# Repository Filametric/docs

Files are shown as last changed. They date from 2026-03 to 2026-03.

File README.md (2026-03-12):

# Filametric Docs

Official documentation for the Filametric DryBase, built with [MkDocs Material](https://squidfunk.github.io/mkdocs-material/).

**Live at:** [docs.filametric.com](https://docs.filametric.com)

## Local development

```bash
pip install mkdocs-material mkdocs-git-revision-date-localized-plugin
mkdocs serve
```

## Deployment

Automatic via GitHub Actions on every push to `main`.

## License

Documentation content © 2026 Filametric B.V. All rights reserved.

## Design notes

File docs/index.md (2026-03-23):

---
hide:
  - navigation
---

# Filametric Documentation

<div class="print-grid" markdown>

<a class="print-card" href="manual/introduction/">
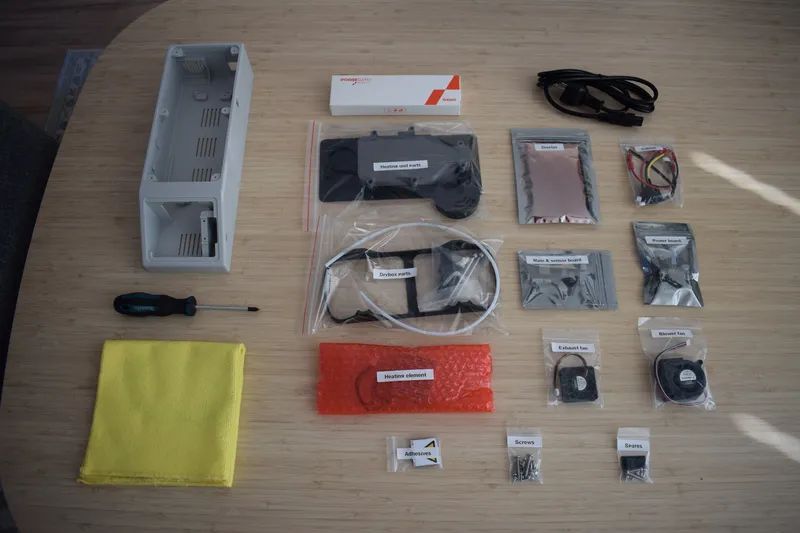
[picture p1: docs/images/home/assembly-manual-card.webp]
Assembly Manual
  
  <span>Assembly Manual</span>
</a>

<a class="print-card" href="3d-printing/guide/">
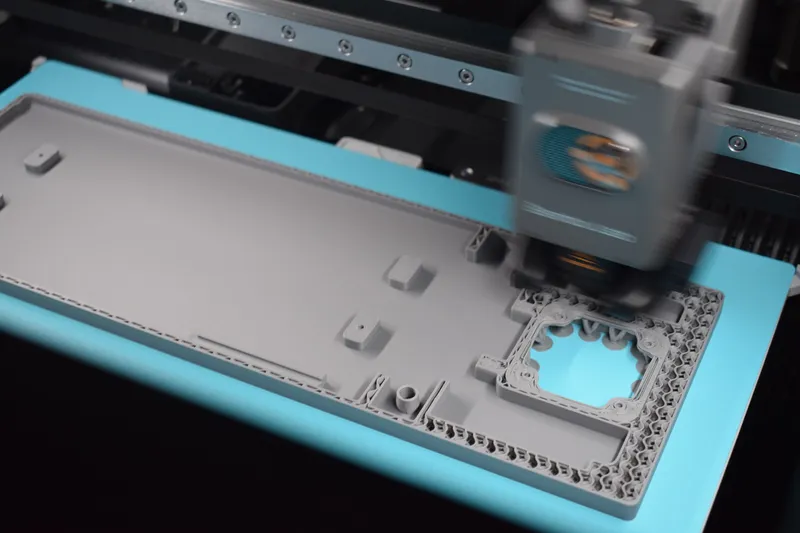
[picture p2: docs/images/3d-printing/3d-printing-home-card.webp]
3D Printing
  
  <span>3D Printing</span>
</a>

<a class="print-card" href="drybase/overview/">
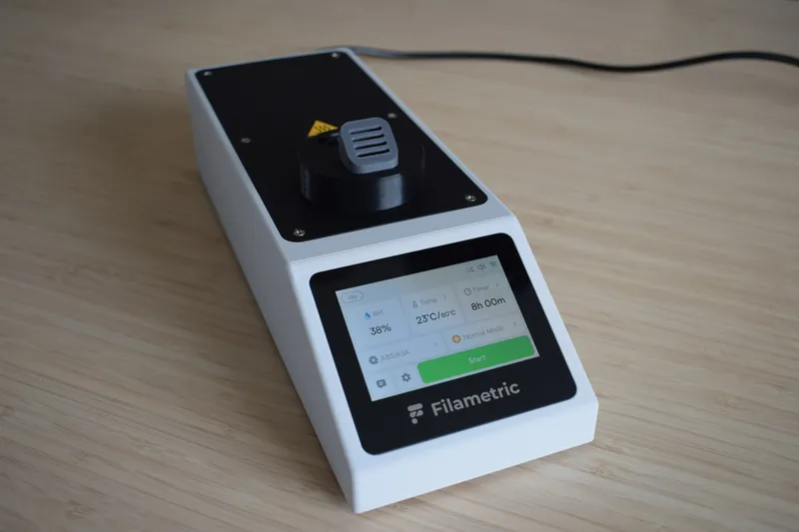
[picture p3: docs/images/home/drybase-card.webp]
DryBase
  
  <span>DryBase</span>
</a>

<a class="print-card" href="drybox/overview/">
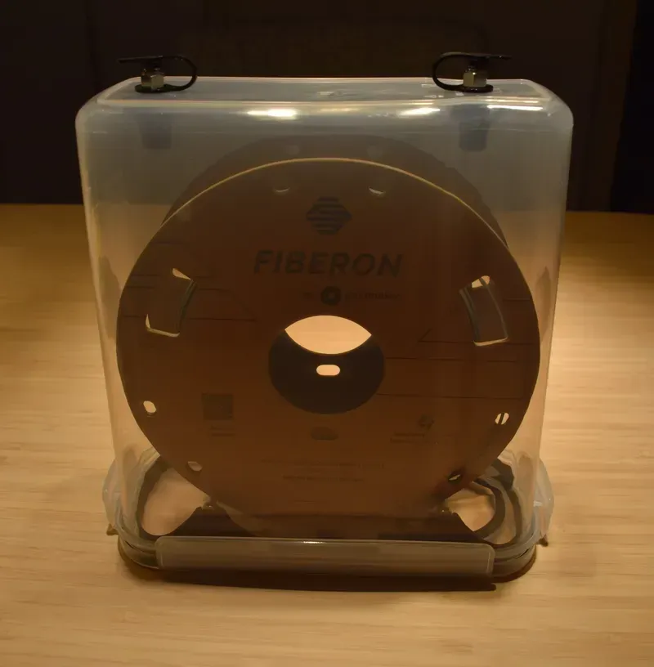
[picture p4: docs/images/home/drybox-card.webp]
Drybox
  
  <span>Drybox</span>
</a>

<a class="print-card" href="studio/overview/">
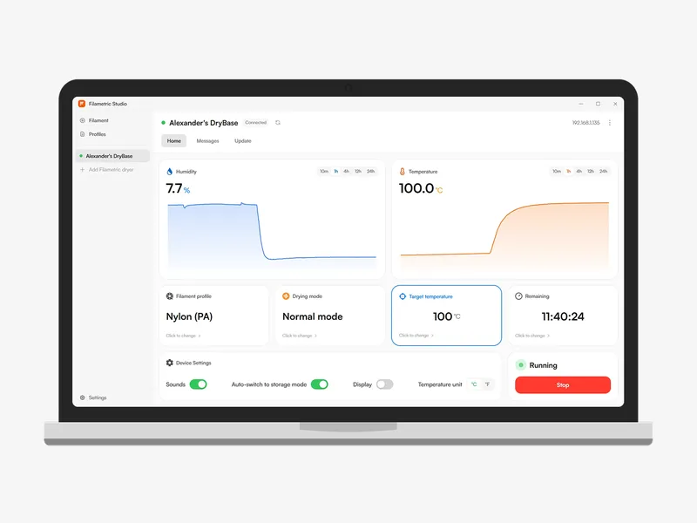
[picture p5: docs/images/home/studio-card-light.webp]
Filametric Studio
  
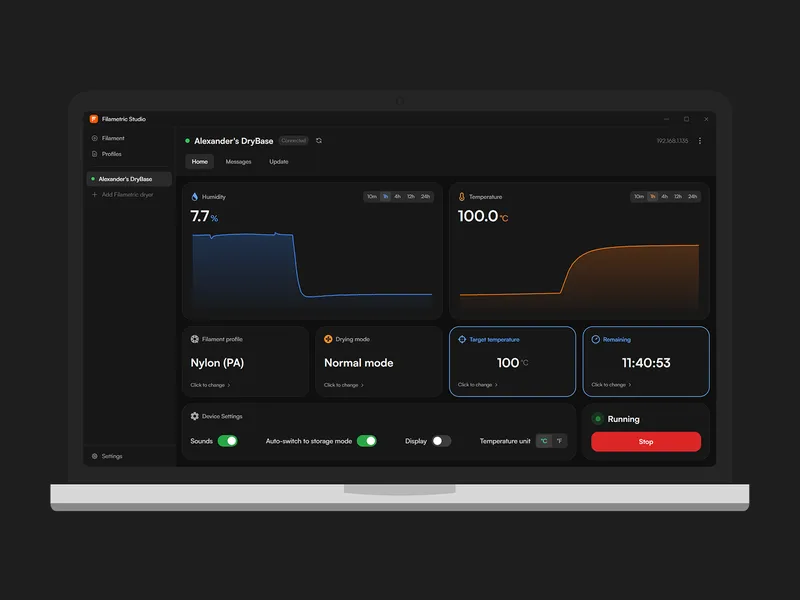
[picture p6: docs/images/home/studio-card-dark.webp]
Filametric Studio
  
  <span>Filametric Studio</span>
</a>

<a class="print-card" href="support/faq/">
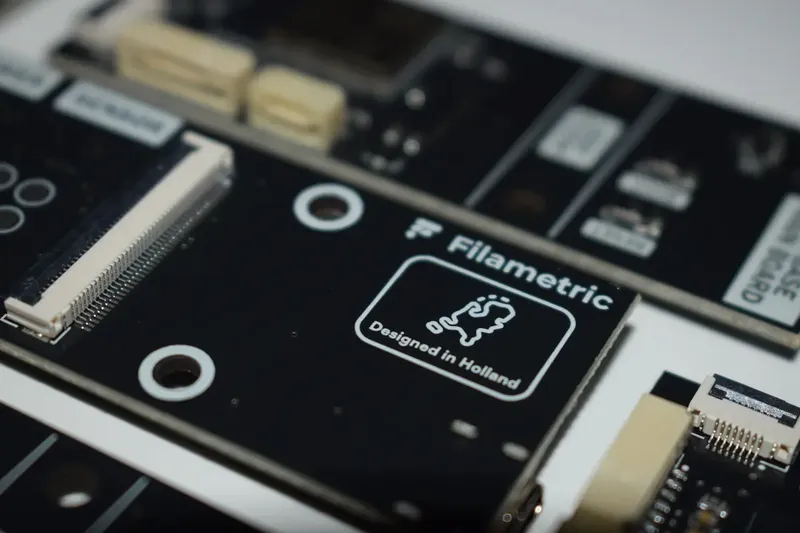
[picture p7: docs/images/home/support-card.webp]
Support
  
  <span>Support</span>
</a>

</div>

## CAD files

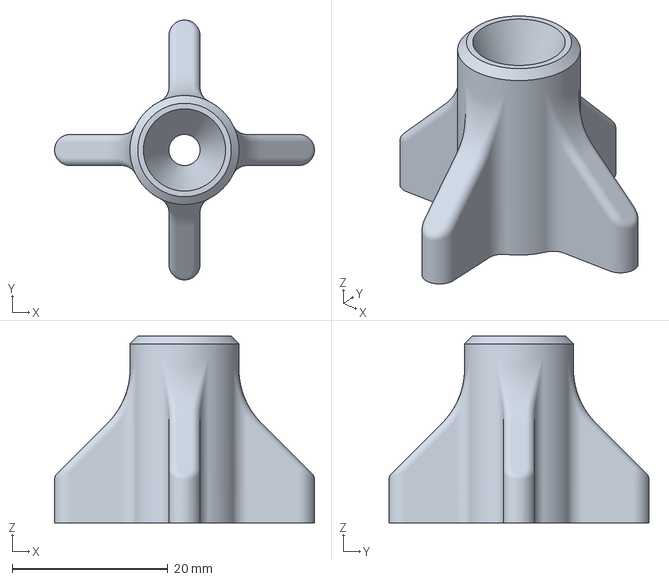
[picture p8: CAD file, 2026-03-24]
docs/downloads/Filametric_Closing_Fastener_3MF.3mf
33.4 x 33.4 x 24.0 mm

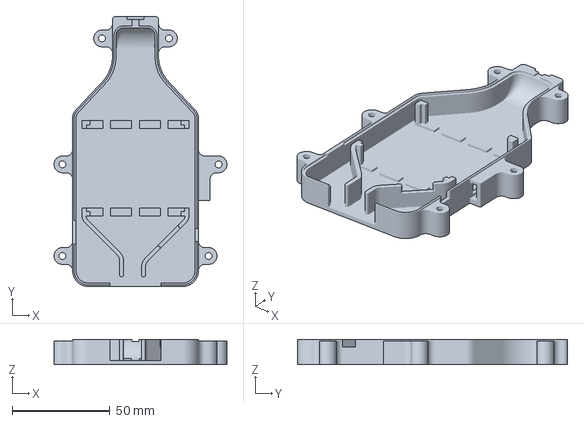
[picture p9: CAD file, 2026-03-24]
docs/downloads/Filametric_Heating_Element_Bottom_Cover_3MF.3mf
88.5 x 138.2 x 12.9 mm

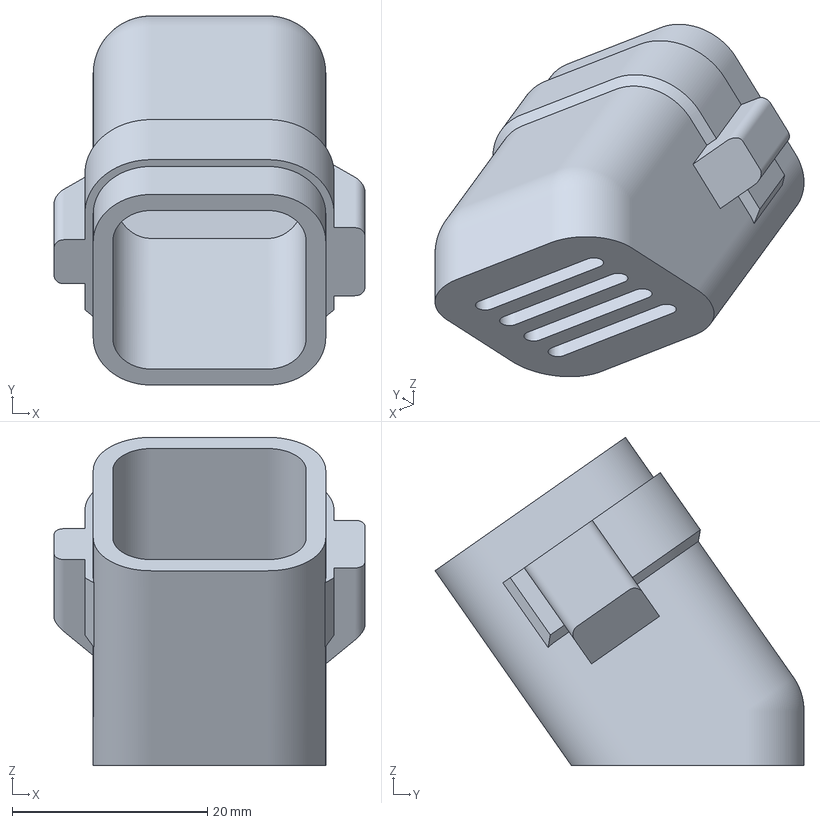
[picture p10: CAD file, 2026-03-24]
docs/downloads/Filametric_Hot_Air_Exhaust_Port_3MF.3mf
31.8 x 37.8 x 33.6 mm

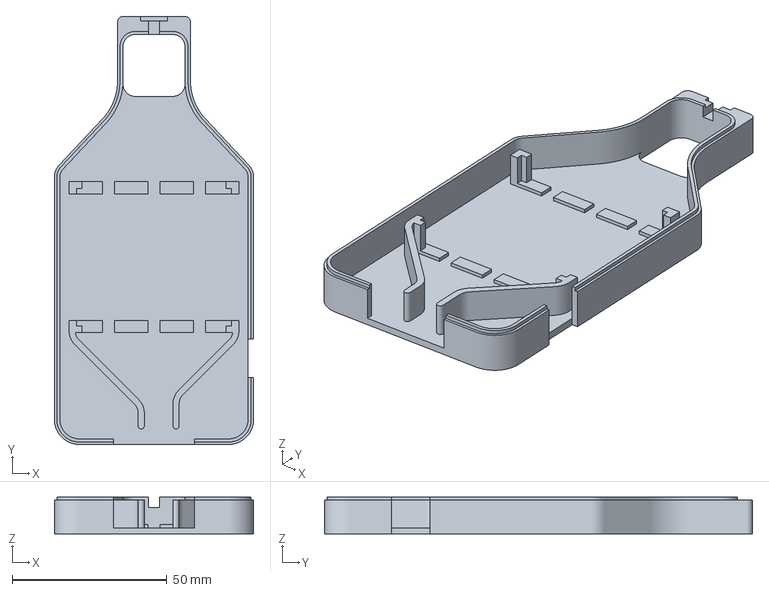
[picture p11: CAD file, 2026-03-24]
docs/downloads/Filametric_Heating_Element_Top_Cover_3MF.3mf
64.4 x 138.2 x 11.9 mm

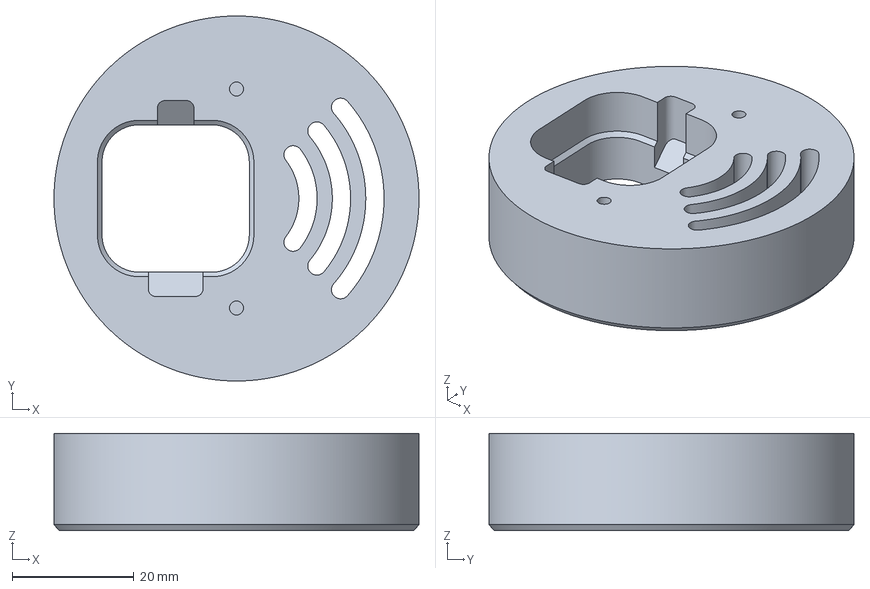
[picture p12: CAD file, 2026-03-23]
docs/downloads/Filametric_Container_Adapter_3MF.3mf
60.0 x 60.0 x 16.0 mm

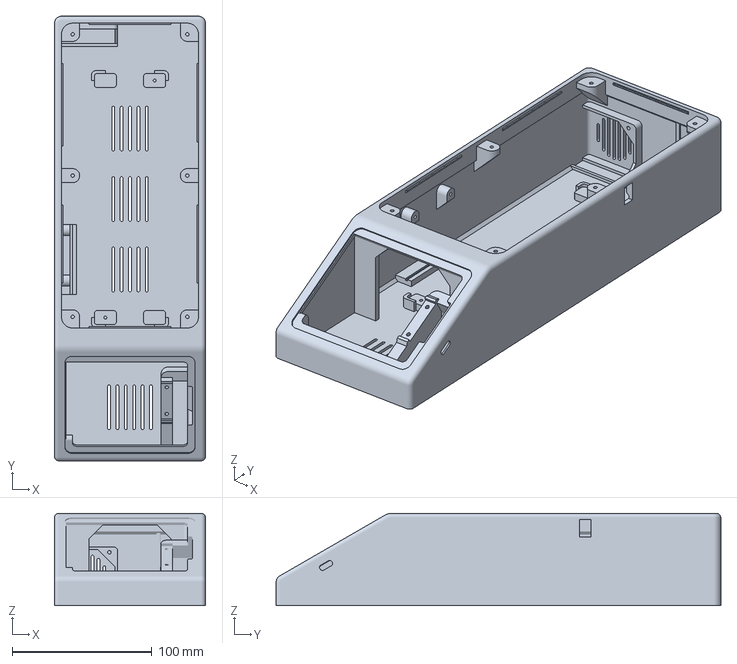
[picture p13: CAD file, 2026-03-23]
docs/downloads/Filametric_Housing_3MF.3mf
108.0 x 318.0 x 66.0 mm

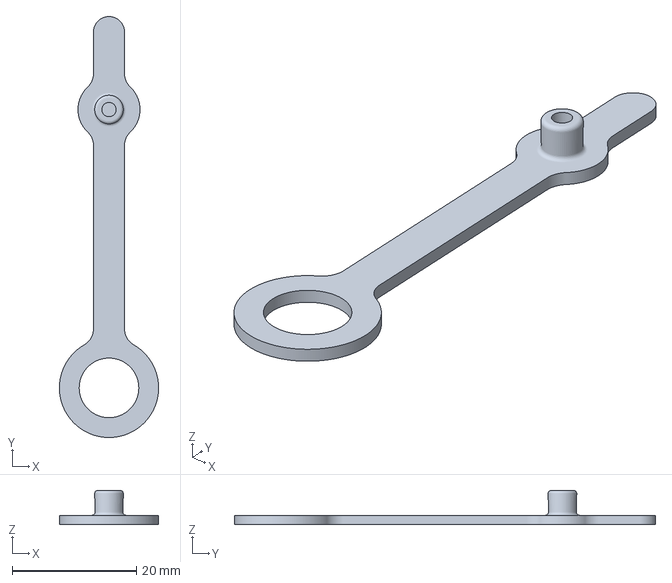
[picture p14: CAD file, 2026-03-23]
docs/downloads/Filametric_Grommet_3MF.3mf
16.0 x 67.9 x 5.50 mm

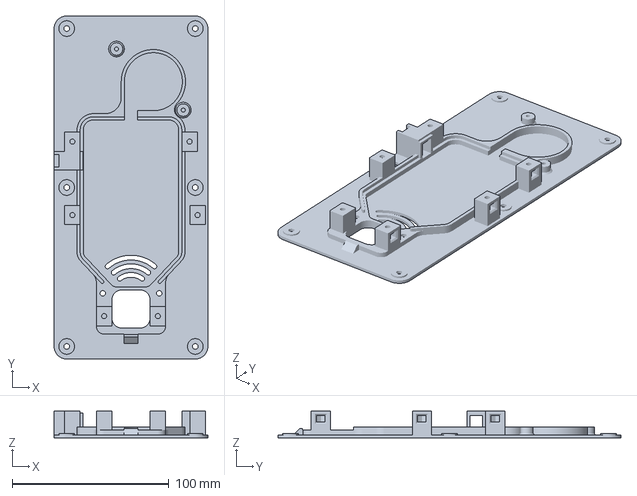
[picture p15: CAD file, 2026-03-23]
docs/downloads/Filametric_Heating_Unit_Baseplate_3MF.3mf
98.1 x 218.8 x 17.2 mm

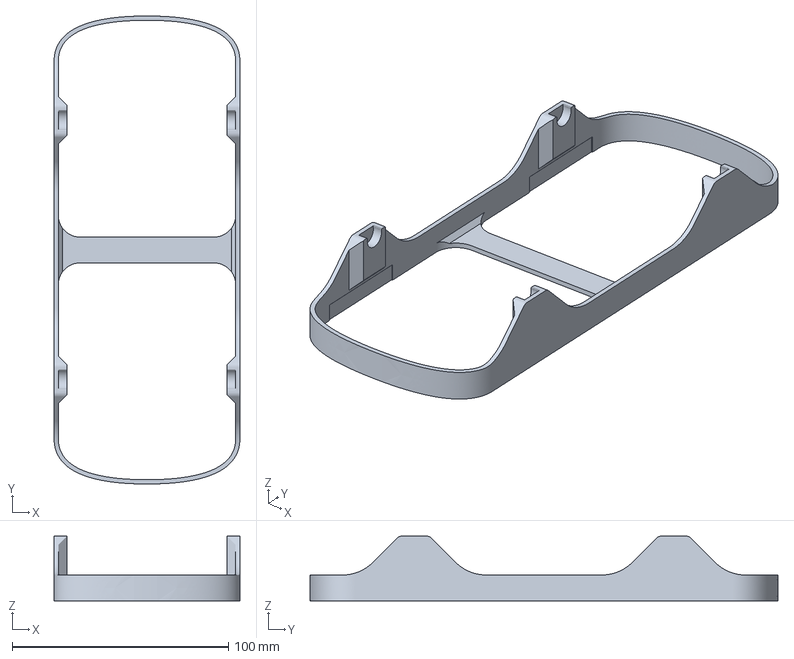
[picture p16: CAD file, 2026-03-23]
docs/downloads/Filametric_Spool_Holder_3MF.3mf
86.0 x 216.5 x 30.0 mm

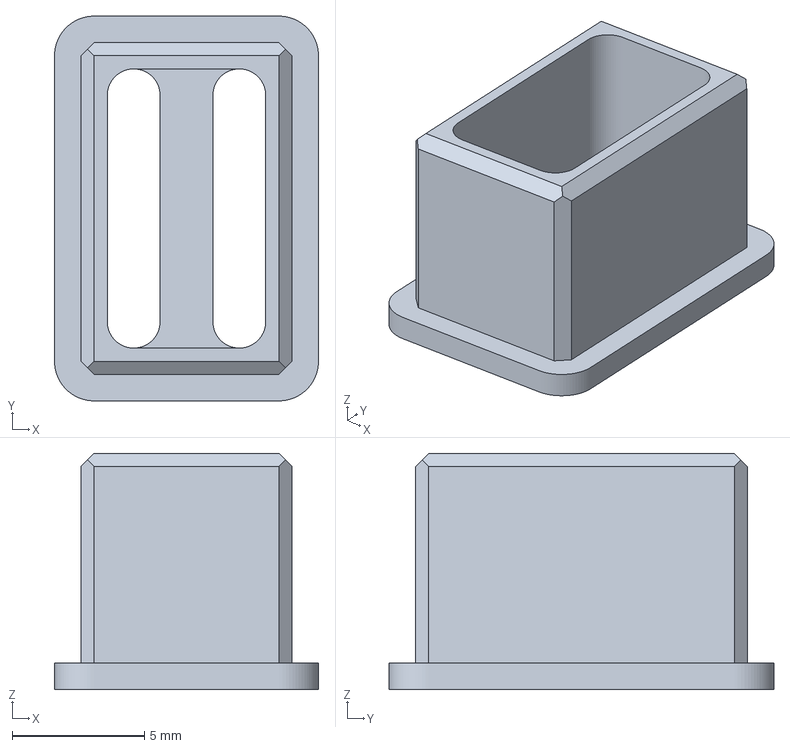
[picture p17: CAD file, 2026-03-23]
docs/downloads/Filametric_Moist_Air_Exhaust_Port_3MF.3mf
10.0 x 14.6 x 8.95 mm

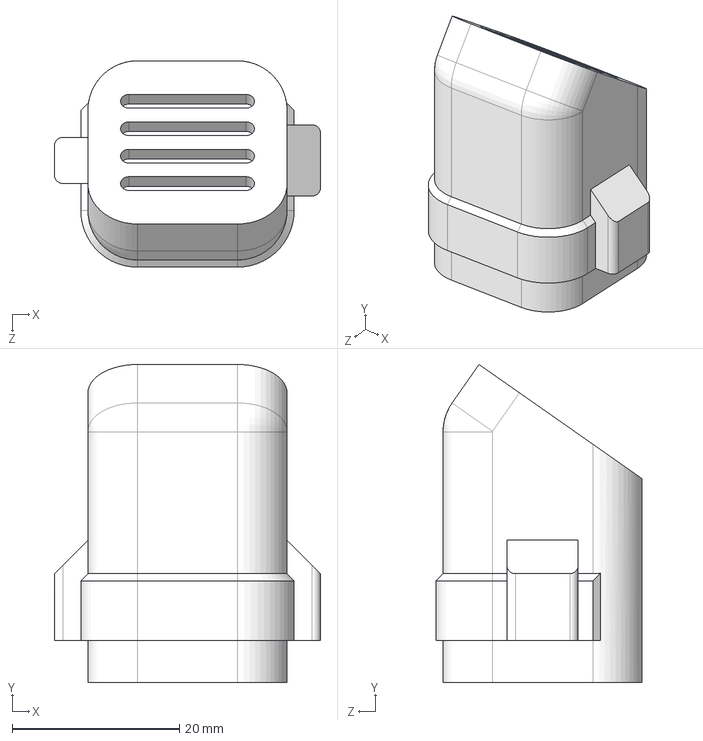
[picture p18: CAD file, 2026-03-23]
docs/downloads/Filametric_Hot_Air_Exhaust_Port_STEP.step
31.8 x 38.0 x 24.6 mm

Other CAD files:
docs/downloads/Filametric_Moist_Air_Exhaust_Port_STEP.step
docs/downloads/Filametric_Spool_Holder_STEP.step
docs/downloads/Filametric_Grommet_STEP.step
docs/downloads/Filametric_Heating_Unit_Baseplate_STEP.step
docs/downloads/Filametric_Heating_Element_Top_Cover_STEP.step
docs/downloads/Filametric_Container_Adapter_STEP.step
docs/downloads/Filametric_Closing_Fastener_STEP.step
docs/downloads/Filametric_Heating_Element_Bottom_Cover_STEP.step
docs/downloads/Filametric_Housing_STEP.step

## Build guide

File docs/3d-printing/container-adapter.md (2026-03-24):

---
comments: true
---
# Container adapter

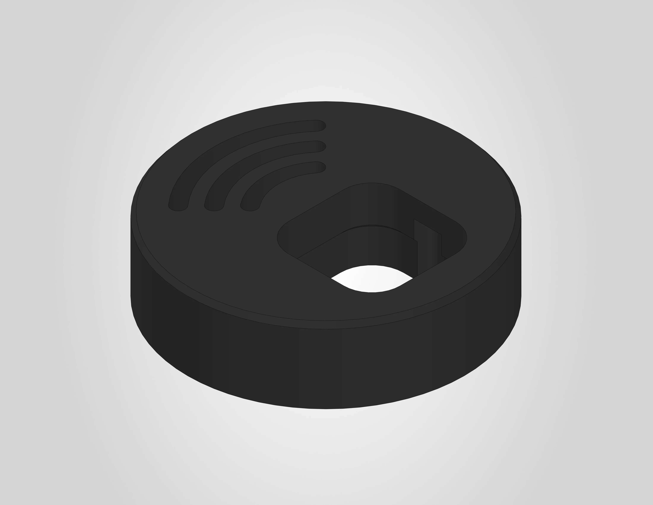
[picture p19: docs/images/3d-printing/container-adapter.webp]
Container adapter


The container adapter connects the drybox container to the heating unit. The 3MF file is pre-configured for a Bambu Lab H2S printer with the settings below already applied. If you are using a different printer, use the settings below as a reference.

A STEP file is also included for users who wish to slice the model independently or adapt it for a different printer.

| | |
|---|---|
| **Dimensions** | 60 x 60 x 16 mm |
| **Estimated print time** | ~33 minutes |
| **Recommended material** | ABS |

---

## Before you print

!!! warning "ABS requires proper ventilation"
    ABS produces fumes during printing. Make sure your printer is enclosed and the room is well ventilated.

!!! warning "Pre-drying is required"
    ABS is sensitive to moisture and **must** be dried before printing. Follow the filament manufacturer's drying instructions.

---

## Filament settings

The .3mf file uses the generic Bambu Lab ABS profile. No parameters were changed from the default profile.

It is recommended to use **ABS**, as this part has been tested and validated with Bambu Lab ABS. Other ABS brands should work as well.

!!! warning "Other materials"
    Other materials may work, but must have at least the same heat resistance as ABS, as these parts are exposed to elevated temperatures during operation. Alternative materials have not been officially tested or validated. Using them is at your own risk and may affect dimensional accuracy and fit.

---

## Workspace settings

The following workspace settings were changed from the default settings:

| Setting | Value |
|---|---|
| Nozzle | **0.4 mm** |
| Layer height | **0.2 mm** |
| Build plate | **Engineering plate** |
| Sparse infill pattern | **Gyroid** |
| Supports | **disabled** |

!!! note "No adhesives needed"
    No glue or other adhesives are required on the engineering plate for this print.

### Modifiers

Two (yellow) modifiers were added to the model to apply 100% infill around the screw hole areas to ensure a strong, reliable connection during assembly. **Do not remove or modify them.**

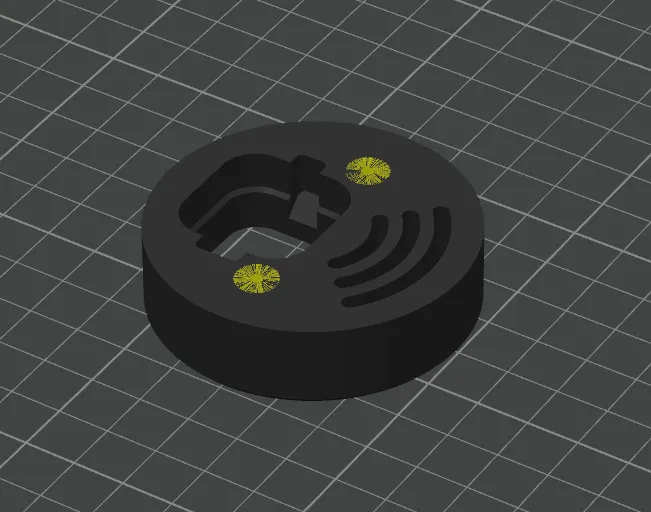
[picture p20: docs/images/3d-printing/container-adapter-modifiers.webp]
Modifiers


The image below shows the sliced result:

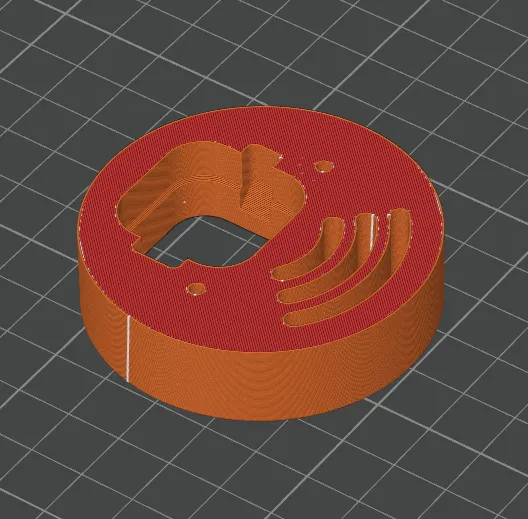
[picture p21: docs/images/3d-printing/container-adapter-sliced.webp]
Sliced result


---

## License & Disclaimer

!!! note "CC BY-NC 4.0"
    All files on this page are licensed under [CC BY-NC 4.0](https://creativecommons.org/licenses/by-nc/4.0/){:target="_blank"}. You are free to download, print, share and adapt them, as long as you credit Filametric and do not use them for commercial purposes. Printing parts for your own personal or business use is permitted. Selling the files, printed parts, or using them to build competing products is not.

!!! warning "Disclaimer"
    These files are provided as-is. Modifications to the model, print settings or orientation may affect fit and function and are at your own risk. See our [Terms of Use](https://filametric.com/terms-of-use){:target="_blank"} for more information.

---

## Downloads

- [:material-download: Container Adapter (.3mf)](../downloads/Filametric_Container_Adapter_3MF.3mf)
- [:material-download: Container Adapter (.step)](../downloads/Filametric_Container_Adapter_STEP.step)

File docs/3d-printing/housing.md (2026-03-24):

---
comments: true
---
# DryBase Housing

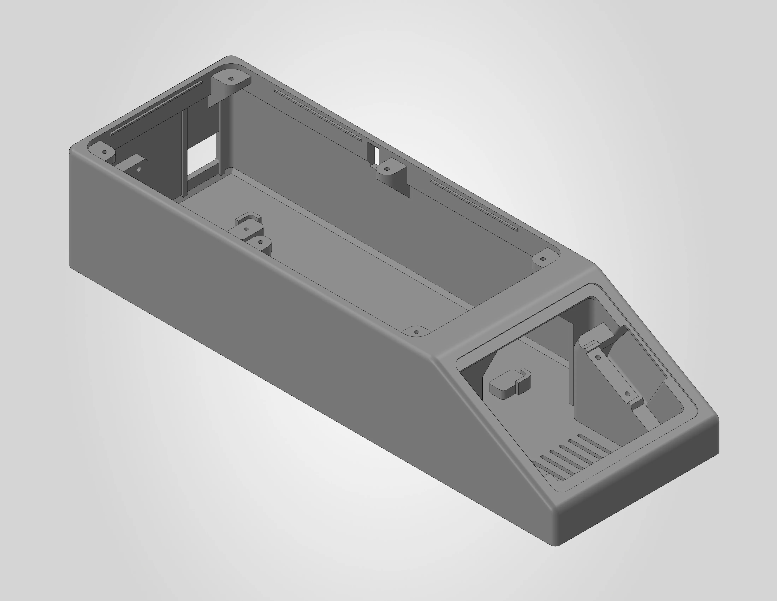
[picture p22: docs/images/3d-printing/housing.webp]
DryBase Housing


The DryBase housing is a single-part print with dimensions of **318 x 108 x 67 mm**. Any printer with a build plate large enough to accommodate these dimensions can be used. The 3MF file is pre-configured for a Bambu Lab H2S printer with the settings below already applied, including modifiers for reinforced screw holes. If you are using a different printer, use the settings below as a reference.

A STEP file is also included for users who wish to slice the model independently or adapt it for a different printer.

| | |
|---|---|
| **Dimensions** | 318 x 108 x 67 mm |
| **Estimated print time** | ~6 hours 8 minutes |
| **Recommended material** | PLA |

---

## Before you print

!!! warning "Clean your build plate"
    Clean your build plate before printing to prevent warping. IPA alone is not sufficient. Wash the textured plate with lukewarm water and dish soap, then dry it thoroughly before placing it on the printer.

!!! note "Pre-drying not required"
    Pre-drying PLA is **not required** for this print.

---

## Filament settings

The .3mf file uses the generic Bambu Lab PLA Basic profile. The only parameter that was changed is the **value for the auxiliary fan, which was set to 0%**. This was done to prevent warping as much as possible.

It is recommended to use **PLA**, as it does not require pre-drying to achieve dimensional accuracy and a quality surface finish. This model has been tested and validated with Bambu Lab PLA Basic, but other PLA brands should work as well.

!!! warning "Other materials"
    Other materials such as PETG or ABS may work if the shrinkage/scaling factor is properly tuned, but have not been officially tested or validated. Using alternative materials is at your own risk and may affect dimensional accuracy, fit and assembly.

---

## Workspace settings

The following workspace settings were changed from the default settings:

| Setting | Value |
|---|---|
| Nozzle | **0.4 mm** |
| Layer height | **0.2 mm** |
| Build plate | **Textured PEI** |
| Sparse infill pattern | **Gyroid** |
| Supports | **enabled** |
| Type of support | **tree (auto)** |
| Support style | **Tree Slim** |

!!! note "No adhesives needed"
    No glue or other adhesives are required on the build plate for this print, as long as the plate is properly cleaned.

### Support blockers

The surface directly above the USB-C port opening was manually painted to disable supports.

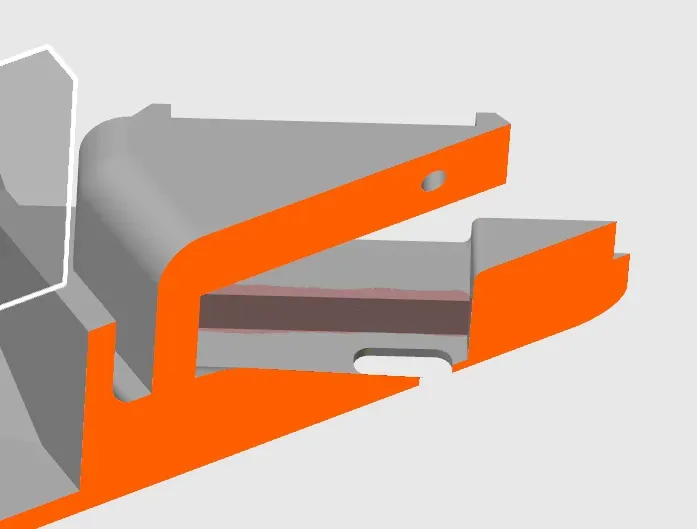
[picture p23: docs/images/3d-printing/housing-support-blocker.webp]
Support blocker


### Modifiers

Two (yellow) modifiers were added to the model to apply 100% infill to the screw hole areas to ensure a strong, reliable connection during assembly. **Do not remove or modify them.**

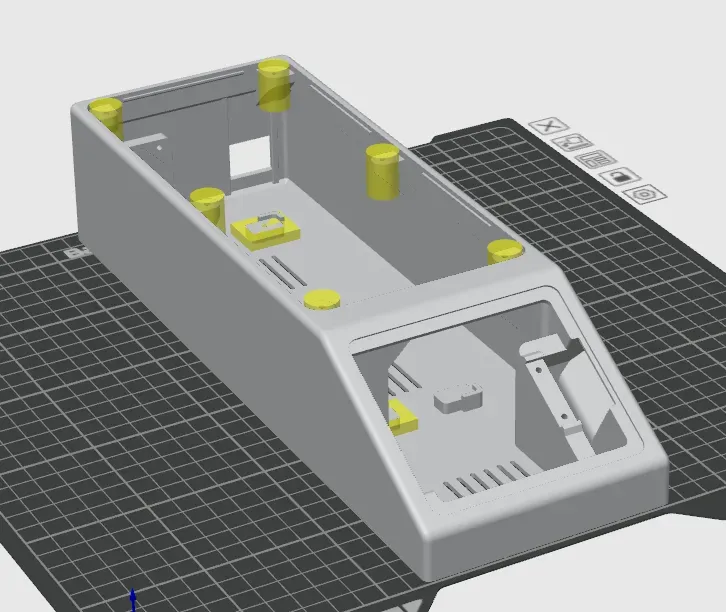
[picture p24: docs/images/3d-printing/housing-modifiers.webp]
Modifiers


The image below shows the sliced result:

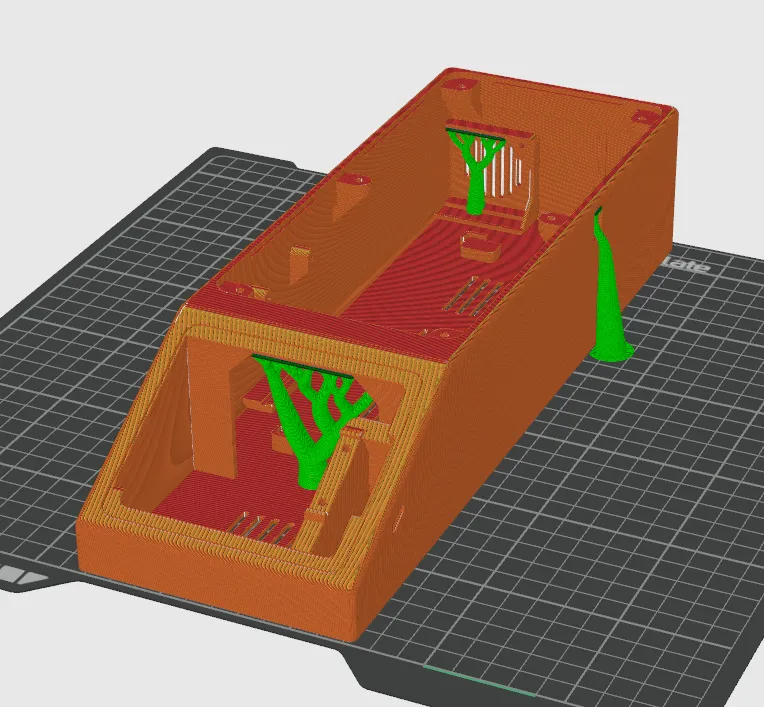
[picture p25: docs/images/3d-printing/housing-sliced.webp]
Sliced result


---

## License & Disclaimer

!!! note "CC BY-NC 4.0"
    All files on this page are licensed under [CC BY-NC 4.0](https://creativecommons.org/licenses/by-nc/4.0/){:target="_blank"}. You are free to download, print, share and adapt them, as long as you credit Filametric and do not use them for commercial purposes. Printing parts for your own personal or business use is permitted. Selling the files, printed parts, or using them to build competing products is not.

!!! warning "Disclaimer"
    These files are provided as-is. Modifications to the model, print settings or orientation may affect fit and function and are at your own risk. See our [Terms of Use](https://filametric.com/terms-of-use){:target="_blank"} for more information.

---

## Downloads

- [:material-download: Housing (.3mf)](../downloads/Filametric_Housing_3MF.3mf)
- [:material-download: Housing (.step)](../downloads/Filametric_Housing_STEP.step)

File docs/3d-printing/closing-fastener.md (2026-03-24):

---
comments: true
---
# Closing fastener

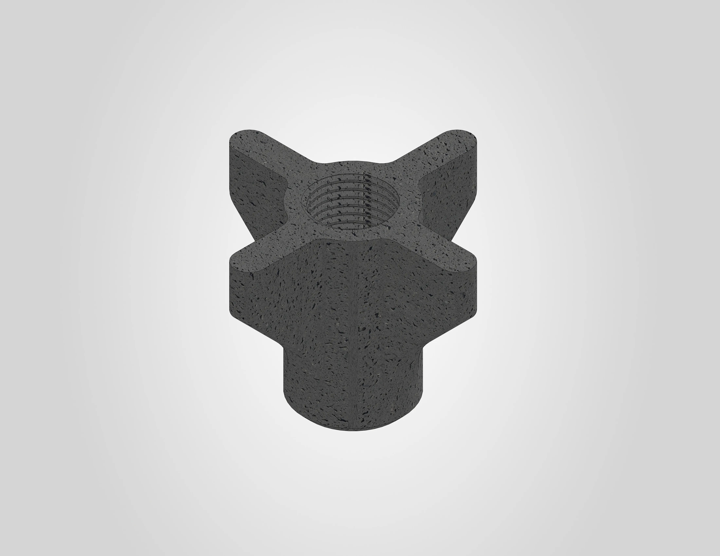
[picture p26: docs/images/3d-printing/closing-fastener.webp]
Closing fastener


The closing fastener secures the pneumatic fittings to the drybox container from the inside. The 3MF file is pre-configured for a Bambu Lab H2S printer with the settings below already applied. If you are using a different printer, use the settings below as a reference.

A STEP file is also included for users who wish to slice the model independently or adapt it for a different printer.

| | |
|---|---|
| **Dimensions** | 33.4 x 33.4 x 24 mm |
| **Estimated print time** | ~9 minutes |
| **Required material** | PA6-GF |

---

## Before you print

!!! warning "Pre-drying is required"
    PA6-GF is extremely sensitive to moisture and **must** be dried before printing. For Polymaker PA6-GF20 Fiberon, dry at **100 °C for at least 12 hours** and keep the filament actively heated at a minimum of **80 °C** during printing to prevent moisture re-absorption. Other PA6-GF variants may have different drying requirements. Always follow the filament manufacturer's instructions.

!!! warning "Proper ventilation required"
    PA6-GF produces fumes during printing. Make sure your printer is enclosed and the room is well ventilated.

---

## Filament settings

The .3mf file uses a modified Bambu Lab PA6-GF profile. The following parameters were changed from the default profile:

| Setting | Value |
|---|---|
| Flow ratio | **0.864** |
| Bed temperature (initial + other layers) | **40 °C** |
| Nozzle temperature (initial + other layers) | **280 °C** |
| Density | **1.2** |
| Chamber temperature | **0 °C (off)** |
| Wipe while retraction | **enabled** |

This part has been tested and validated with **Polymaker PA6-GF20 Fiberon**. This is currently the only verified filament for this component.

!!! note "Printer-specific settings"
    The flow ratio of **0.864** was calibrated on a Bambu Lab H2S and may vary depending on your printer. The bed temperature of **40 °C** and disabled chamber heating are specifically tuned for Fiberon's warp-free technology. Other PA6-GF variants may require different flow ratios, bed and chamber temperatures. Always calibrate for your setup.

!!! warning "No alternative material types"
    This part is directly exposed to high temperatures during operation. Do **not** use PLA, PETG, ABS or other materials with a lower heat deflection temperature. Using an unsuitable material may result in deformation, failure, or a safety hazard. Other PA6-GF brands may work, but have not been officially tested or validated.

---

## Workspace settings

The following workspace settings were changed from the default settings:

| Setting | Value |
|---|---|
| Nozzle | **0.4 mm** |
| Layer height | **0.2 mm** |
| Build plate | **Engineering plate** |
| Sparse infill pattern | **Gyroid** |
| Supports | **disabled** |

!!! note "No adhesives needed"
    No glue or other adhesives are required on the engineering plate for this print.

The image below shows the sliced result:

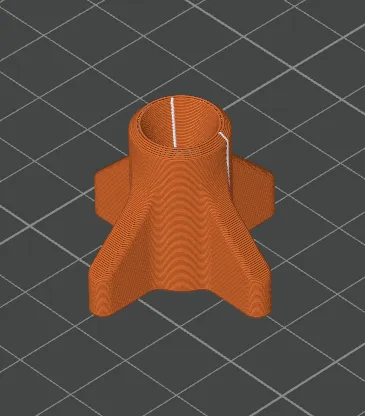
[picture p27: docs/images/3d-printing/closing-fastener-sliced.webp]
Sliced result


---

## License & Disclaimer

!!! note "CC BY-NC 4.0"
    All files on this page are licensed under [CC BY-NC 4.0](https://creativecommons.org/licenses/by-nc/4.0/){:target="_blank"}. You are free to download, print, share and adapt them, as long as you credit Filametric and do not use them for commercial purposes. Printing parts for your own personal or business use is permitted. Selling the files, printed parts, or using them to build competing products is not.

!!! warning "Disclaimer"
    These files are provided as-is. Modifications to the model, print settings or orientation may affect fit and function and are at your own risk. See our [Terms of Use](https://filametric.com/terms-of-use){:target="_blank"} for more information.

---

## Downloads

- [:material-download: Closing Fastener (.3mf)](../downloads/Filametric_Closing_Fastener_3MF.3mf)
- [:material-download: Closing Fastener (.step)](../downloads/Filametric_Closing_Fastener_STEP.step)

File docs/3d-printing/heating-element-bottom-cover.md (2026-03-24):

---
comments: true
---
# Heating element bottom cover

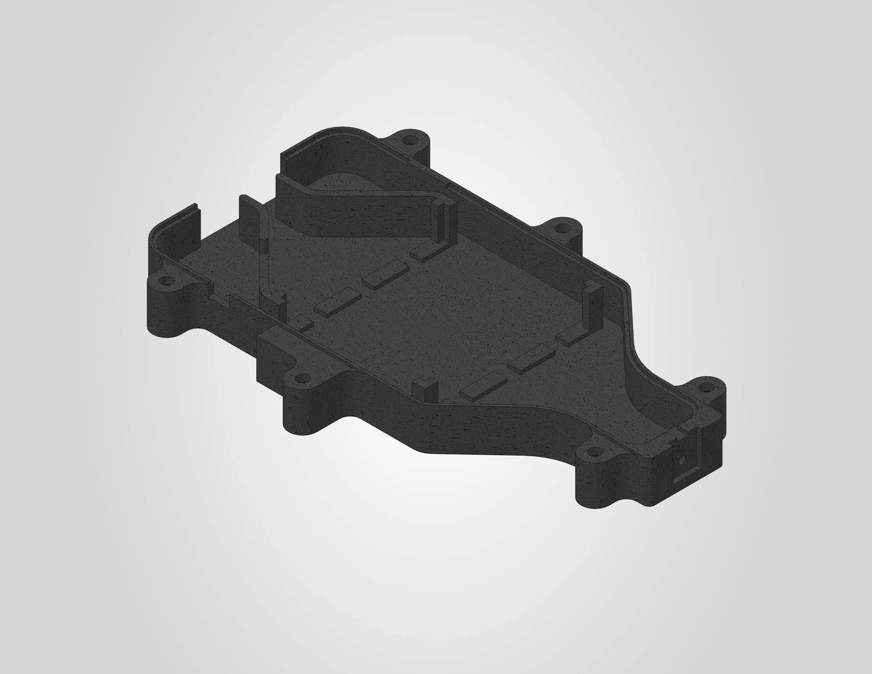
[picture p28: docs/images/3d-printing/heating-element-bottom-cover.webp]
Heating element bottom cover


The heating element bottom cover encloses the heating element from below and is directly exposed to high temperatures during operation. This part **must** be printed in a high-temperature resistant material. The 3MF file is pre-configured for a Bambu Lab H2S printer with the settings below already applied. If you are using a different printer, use the settings below as a reference.

A STEP file is also included for users who wish to slice the model independently or adapt it for a different printer.

| | |
|---|---|
| **Dimensions** | 88.5 x 138.2 x 12.9 mm |
| **Estimated print time** | ~1 hour |
| **Required material** | PA6-GF |

---

## Before you print

!!! warning "Pre-drying is required"
    PA6-GF is extremely sensitive to moisture and **must** be dried before printing. For Polymaker PA6-GF20 Fiberon, dry at **100 °C for at least 12 hours** and keep the filament actively heated at a minimum of **80 °C** during printing to prevent moisture re-absorption. Other PA6-GF variants may have different drying requirements. Always follow the filament manufacturer's instructions.

!!! warning "Proper ventilation required"
    PA6-GF produces fumes during printing. Make sure your printer is enclosed and the room is well ventilated.

---

## Filament settings

The .3mf file uses a modified Bambu Lab PA6-GF profile. The following parameters were changed from the default profile:

| Setting | Value |
|---|---|
| Flow ratio | **0.864** |
| Bed temperature (initial + other layers) | **40 °C** |
| Nozzle temperature (initial + other layers) | **280 °C** |
| Density | **1.2** |
| Chamber temperature | **0 °C (off)** |
| Wipe while retraction | **enabled** |

This part has been tested and validated with **Polymaker PA6-GF20 Fiberon**. This is currently the only verified filament for this component.

!!! note "Printer-specific settings"
    The flow ratio of **0.864** was calibrated on a Bambu Lab H2S and may vary depending on your printer. The bed temperature of **40 °C** and disabled chamber heating are specifically tuned for Fiberon's warp-free technology. Other PA6-GF variants may require different flow ratios, bed and chamber temperatures. Always calibrate for your setup.

!!! warning "No alternative material types"
    This part is directly exposed to high temperatures during operation. Do **not** use PLA, PETG, ABS or other materials with a lower heat deflection temperature. Using an unsuitable material may result in deformation, failure, or a safety hazard. Other PA6-GF brands may work, but have not been officially tested or validated.

---

## Workspace settings

The following workspace settings were changed from the default settings:

| Setting | Value |
|---|---|
| Nozzle | **0.4 mm** |
| Layer height | **0.2 mm** |
| Build plate | **Engineering plate** |
| Sparse infill pattern | **Gyroid** |
| Seam position | **nearest** |
| Supports | **disabled** |

!!! note "No adhesives needed"
    No glue or other adhesives are required on the engineering plate for this print.

The image below shows the sliced result:

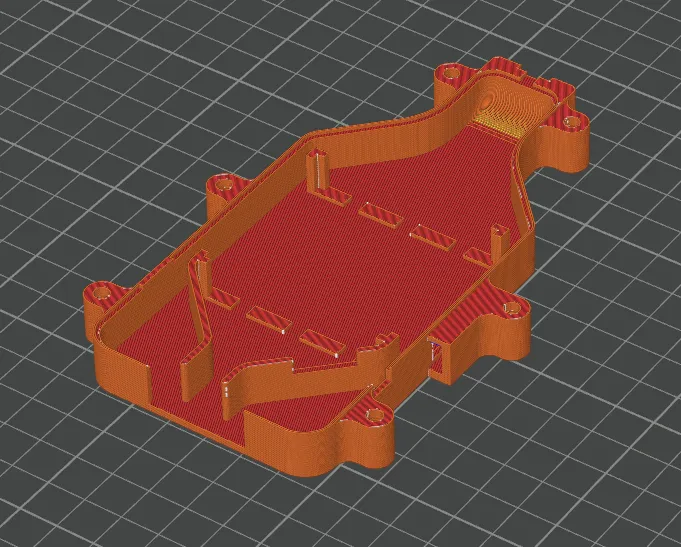
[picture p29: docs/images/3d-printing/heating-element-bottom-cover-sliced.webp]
Sliced result


---

## License & Disclaimer

!!! note "CC BY-NC 4.0"
    All files on this page are licensed under [CC BY-NC 4.0](https://creativecommons.org/licenses/by-nc/4.0/){:target="_blank"}. You are free to download, print, share and adapt them, as long as you credit Filametric and do not use them for commercial purposes. Printing parts for your own personal or business use is permitted. Selling the files, printed parts, or using them to build competing products is not.

!!! warning "Disclaimer"
    These files are provided as-is. Modifications to the model, print settings or orientation may affect fit and function and are at your own risk. See our [Terms of Use](https://filametric.com/terms-of-use){:target="_blank"} for more information.

---

## Downloads

- [:material-download: Heating Element Bottom Cover (.3mf)](../downloads/Filametric_Heating_Element_Bottom_Cover_3MF.3mf)
- [:material-download: Heating Element Bottom Cover (.step)](../downloads/Filametric_Heating_Element_Bottom_Cover_STEP.step)

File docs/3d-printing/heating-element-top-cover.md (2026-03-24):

---
comments: true
---
# Heating element top cover

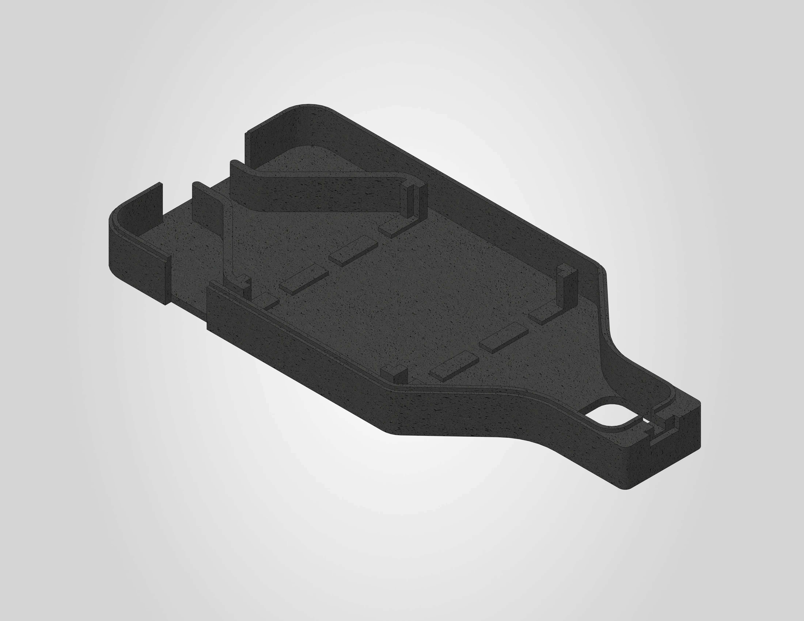
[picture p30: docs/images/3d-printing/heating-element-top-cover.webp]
Heating element top cover


The heating element top cover encloses the heating element from above and is directly exposed to high temperatures during operation. This part **must** be printed in a high-temperature resistant material. The 3MF file is pre-configured for a Bambu Lab H2S printer with the settings below already applied. If you are using a different printer, use the settings below as a reference.

A STEP file is also included for users who wish to slice the model independently or adapt it for a different printer.

| | |
|---|---|
| **Dimensions** | 64.4 x 138.2 x 11.9 mm |
| **Estimated print time** | ~43 minutes |
| **Required material** | PA6-GF |

---

## Before you print

!!! warning "Pre-drying is required"
    PA6-GF is extremely sensitive to moisture and **must** be dried before printing. For Polymaker PA6-GF20 Fiberon, dry at **100 °C for at least 12 hours** and keep the filament actively heated at a minimum of **80 °C** during printing to prevent moisture re-absorption. Other PA6-GF variants may have different drying requirements. Always follow the filament manufacturer's instructions.

!!! warning "Proper ventilation required"
    PA6-GF produces fumes during printing. Make sure your printer is enclosed and the room is well ventilated.

---

## Filament settings

The .3mf file uses a modified Bambu Lab PA6-GF profile. The following parameters were changed from the default profile:

| Setting | Value |
|---|---|
| Flow ratio | **0.864** |
| Bed temperature (initial + other layers) | **40 °C** |
| Nozzle temperature (initial + other layers) | **280 °C** |
| Density | **1.2** |
| Chamber temperature | **0 °C (off)** |
| Wipe while retraction | **enabled** |

This part has been tested and validated with **Polymaker PA6-GF20 Fiberon**. This is currently the only verified filament for this component.

!!! note "Printer-specific settings"
    The flow ratio of **0.864** was calibrated on a Bambu Lab H2S and may vary depending on your printer. The bed temperature of **40 °C** and disabled chamber heating are specifically tuned for Fiberon's warp-free technology. Other PA6-GF variants may require different flow ratios, bed and chamber temperatures. Always calibrate for your setup.

!!! warning "No alternative material types"
    This part is directly exposed to high temperatures during operation. Do **not** use PLA, PETG, ABS or other materials with a lower heat deflection temperature. Using an unsuitable material may result in deformation, failure, or a safety hazard. Other PA6-GF brands may work, but have not been officially tested or validated.

---

## Workspace settings

The following workspace settings were changed from the default settings:

| Setting | Value |
|---|---|
| Nozzle | **0.4 mm** |
| Layer height | **0.2 mm** |
| Build plate | **Engineering plate** |
| Sparse infill pattern | **Gyroid** |
| Seam position | **nearest** |
| Supports | **disabled** |

!!! note "No adhesives needed"
    No glue or other adhesives are required on the engineering plate for this print.

The image below shows the sliced result:

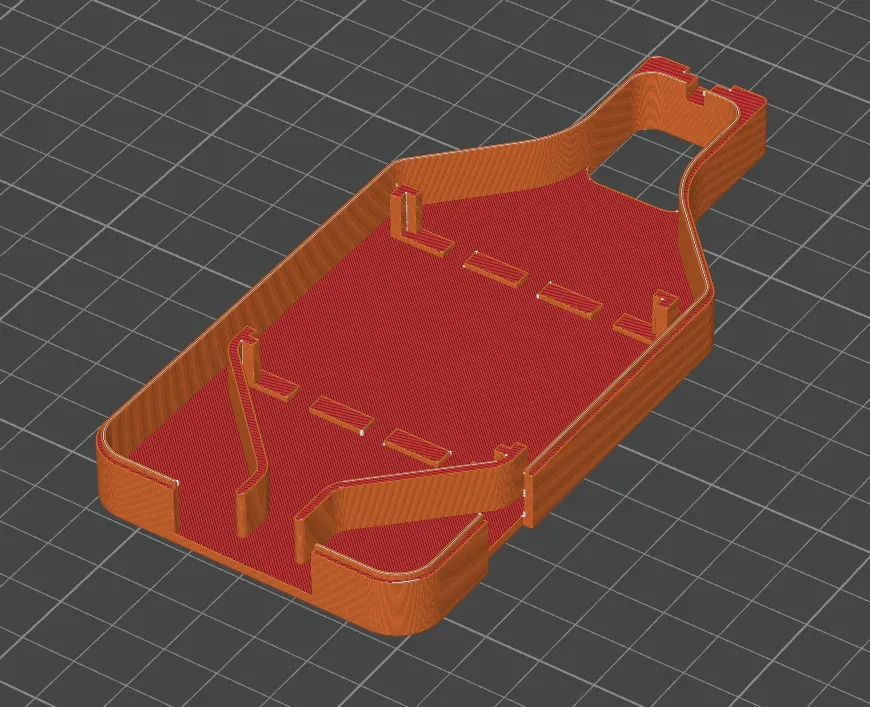
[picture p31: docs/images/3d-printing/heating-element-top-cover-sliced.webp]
Sliced result


---

## License & Disclaimer

!!! note "CC BY-NC 4.0"
    All files on this page are licensed under [CC BY-NC 4.0](https://creativecommons.org/licenses/by-nc/4.0/){:target="_blank"}. You are free to download, print, share and adapt them, as long as you credit Filametric and do not use them for commercial purposes. Printing parts for your own personal or business use is permitted. Selling the files, printed parts, or using them to build competing products is not.

!!! warning "Disclaimer"
    These files are provided as-is. Modifications to the model, print settings or orientation may affect fit and function and are at your own risk. See our [Terms of Use](https://filametric.com/terms-of-use){:target="_blank"} for more information.

---

## Downloads

- [:material-download: Heating Element Top Cover (.3mf)](../downloads/Filametric_Heating_Element_Top_Cover_3MF.3mf)
- [:material-download: Heating Element Top Cover (.step)](../downloads/Filametric_Heating_Element_Top_Cover_STEP.step)

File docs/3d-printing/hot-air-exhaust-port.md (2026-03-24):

---
comments: true
---
# Hot air exhaust port

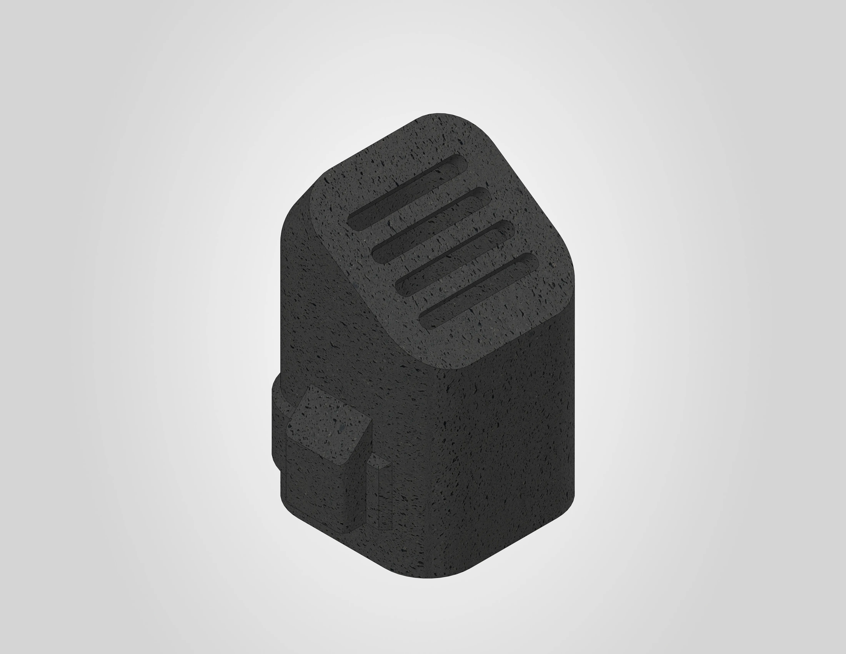
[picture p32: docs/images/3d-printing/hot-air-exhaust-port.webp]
Hot air exhaust port


The hot air exhaust port channels heated air out of the heating unit and is directly exposed to high temperatures during operation. This part **must** be printed in a high-temperature resistant material. The 3MF file is pre-configured for a Bambu Lab H2S printer with the settings below already applied. If you are using a different printer, use the settings below as a reference.

A STEP file is also included for users who wish to slice the model independently or adapt it for a different printer.

| | |
|---|---|
| **Dimensions** | 31.8 x 37.8 x 33.6 mm |
| **Estimated print time** | ~16 minutes |
| **Required material** | PA6-GF |

---

## Before you print

!!! warning "Pre-drying is required"
    PA6-GF is extremely sensitive to moisture and **must** be dried before printing. For Polymaker PA6-GF20 Fiberon, dry at **100 °C for at least 12 hours** and keep the filament actively heated at a minimum of **80 °C** during printing to prevent moisture re-absorption. Other PA6-GF variants may have different drying requirements. Always follow the filament manufacturer's instructions.

!!! warning "Proper ventilation required"
    PA6-GF produces fumes during printing. Make sure your printer is enclosed and the room is well ventilated.

---

## Filament settings

The .3mf file uses a modified Bambu Lab PA6-GF profile. The following parameters were changed from the default profile:

| Setting | Value |
|---|---|
| Flow ratio | **0.864** |
| Bed temperature (initial + other layers) | **40 °C** |
| Nozzle temperature (initial + other layers) | **280 °C** |
| Density | **1.2** |
| Chamber temperature | **0 °C (off)** |
| Wipe while retraction | **enabled** |

This part has been tested and validated with **Polymaker PA6-GF20 Fiberon**. This is currently the only verified filament for this component.

!!! note "Printer-specific settings"
    The flow ratio of **0.864** was calibrated on a Bambu Lab H2S and may vary depending on your printer. The bed temperature of **40 °C** and disabled chamber heating are specifically tuned for Fiberon's warp-free technology. Other PA6-GF variants may require different flow ratios, bed and chamber temperatures. Always calibrate for your setup.

!!! warning "No alternative material types"
    This part is directly exposed to high temperatures during operation. Do **not** use PLA, PETG, ABS or other materials with a lower heat deflection temperature. Using an unsuitable material may result in deformation, failure, or a safety hazard. Other PA6-GF brands may work, but have not been officially tested or validated.

---

## Workspace settings

The following workspace settings were changed from the default settings:

| Setting | Value |
|---|---|
| Nozzle | **0.4 mm** |
| Layer height | **0.2 mm** |
| Build plate | **Engineering plate** |
| Sparse infill pattern | **Gyroid** |
| Supports | **disabled** |

!!! note "No adhesives needed"
    No glue or other adhesives are required on the engineering plate for this print.

The image below shows the sliced result:

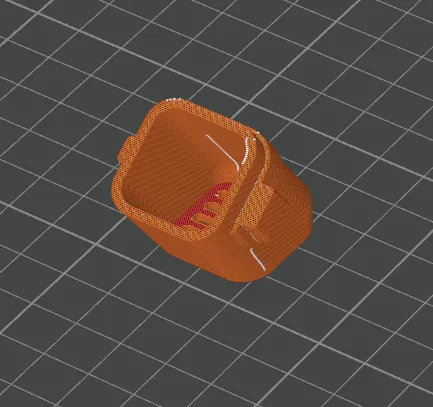
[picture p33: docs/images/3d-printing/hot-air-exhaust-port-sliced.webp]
Sliced result


---

## License & Disclaimer

!!! note "CC BY-NC 4.0"
    All files on this page are licensed under [CC BY-NC 4.0](https://creativecommons.org/licenses/by-nc/4.0/){:target="_blank"}. You are free to download, print, share and adapt them, as long as you credit Filametric and do not use them for commercial purposes. Printing parts for your own personal or business use is permitted. Selling the files, printed parts, or using them to build competing products is not.

!!! warning "Disclaimer"
    These files are provided as-is. Modifications to the model, print settings or orientation may affect fit and function and are at your own risk. See our [Terms of Use](https://filametric.com/terms-of-use){:target="_blank"} for more information.

---

## Downloads

- [:material-download: Hot Air Exhaust Port (.3mf)](../downloads/Filametric_Hot_Air_Exhaust_Port_3MF.3mf)
- [:material-download: Hot Air Exhaust Port (.step)](../downloads/Filametric_Hot_Air_Exhaust_Port_STEP.step)

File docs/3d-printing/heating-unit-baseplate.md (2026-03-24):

---
comments: true
---
# Heating unit baseplate

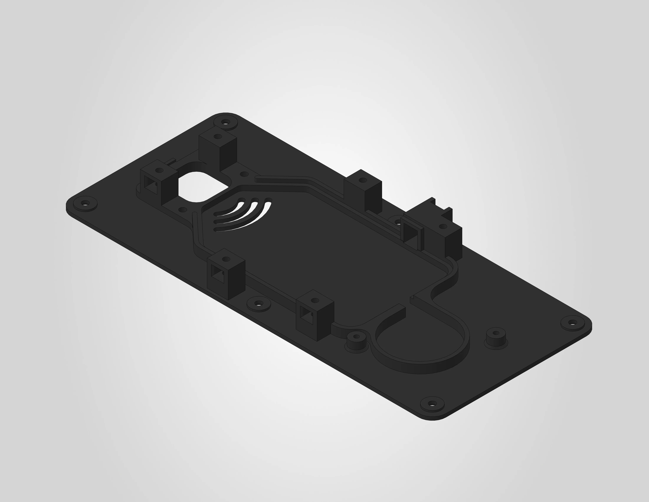
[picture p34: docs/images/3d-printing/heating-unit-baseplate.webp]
Heating unit baseplate


The heating unit baseplate is the main structural part of the heating unit assembly. The 3MF file is pre-configured for a Bambu Lab H2S printer with the settings below already applied. If you are using a different printer, use the settings below as a reference.

A STEP file is also included for users who wish to slice the model independently or adapt it for a different printer.

| | |
|---|---|
| **Dimensions** | 218.8 x 98.1 x 17.2 mm |
| **Estimated print time** | ~1 hour 41 minutes |
| **Recommended material** | ABS |

---

## Before you print

!!! warning "Clean your build plate"
    Clean your build plate before printing to prevent warping. Wash the engineering plate with lukewarm water and dish soap, then dry it thoroughly before placing it on the printer.

!!! warning "ABS requires proper ventilation"
    ABS produces fumes during printing. Make sure your printer is enclosed and the room is well ventilated.

!!! warning "Pre-drying is required"
    ABS is sensitive to moisture and **must** be dried before printing. Follow the filament manufacturer's drying instructions.

---

## Filament settings

The .3mf file uses the generic Bambu Lab ABS profile. No parameters were changed from the default profile.

It is recommended to use **ABS**, as this part has been tested and validated with Bambu Lab ABS. Other ABS brands should work as well.

!!! warning "Other materials"
    Other materials may work, but must have at least the same heat resistance as ABS, as these parts are exposed to elevated temperatures during operation. Alternative materials have not been officially tested or validated. Using them is at your own risk and may affect dimensional accuracy and fit.

---

## Workspace settings

The following workspace settings were changed from the default settings:

| Setting | Value |
|---|---|
| Nozzle | **0.4 mm** |
| Layer height | **0.2 mm** |
| Build plate | **Engineering plate** |
| Sparse infill pattern | **Gyroid** |
| Supports | **enabled** |
| Type of support | **tree (auto)** |
| Support style | **Default** |

!!! note "No adhesives needed"
    No glue or other adhesives are required on the engineering plate for this print.

### Support blockers

The baseplate has six nut pockets with cavities underneath. Support blockers have been manually painted inside these cavities to prevent support material from being generated there, as it would be very difficult to remove after printing. The support material in the nut pockets themselves is left in place and can be removed easily.

The image below shows the six cavities highlighted with red circles. The small red dots inside each cavity are the manually painted support blockers:

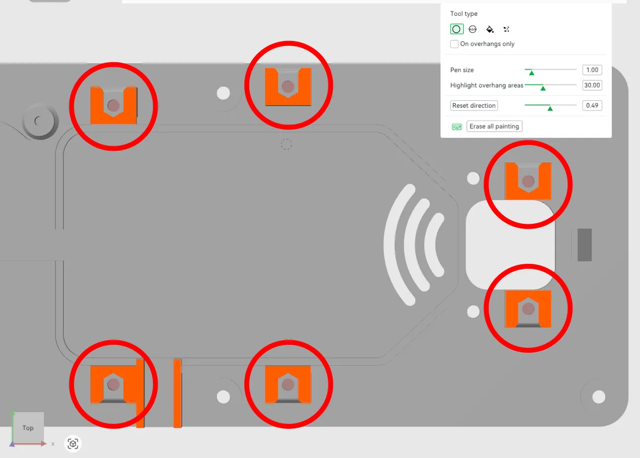
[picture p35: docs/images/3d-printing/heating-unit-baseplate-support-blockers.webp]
Support blockers


The image below shows the sliced result:

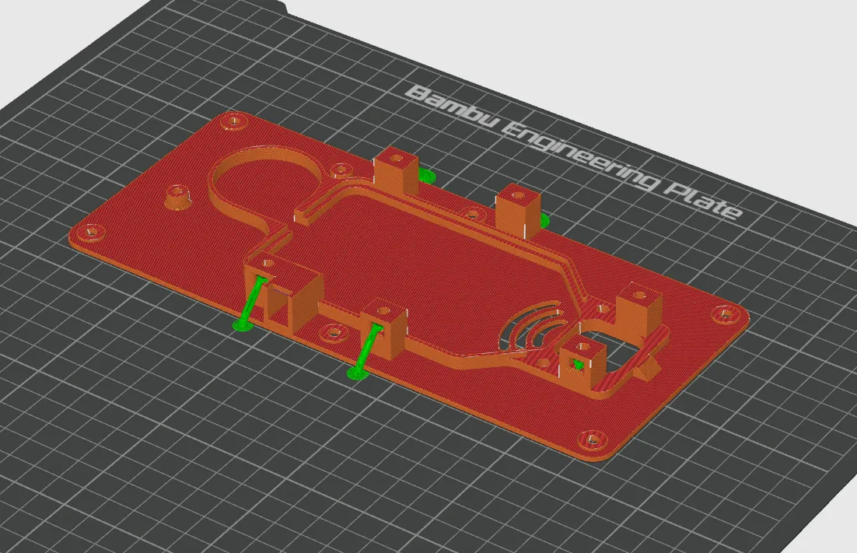
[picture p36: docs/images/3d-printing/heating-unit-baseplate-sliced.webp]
Sliced result


**Do not remove or modify the support blockers in the 3MF file.**

---

## License & Disclaimer

!!! note "CC BY-NC 4.0"
    All files on this page are licensed under [CC BY-NC 4.0](https://creativecommons.org/licenses/by-nc/4.0/){:target="_blank"}. You are free to download, print, share and adapt them, as long as you credit Filametric and do not use them for commercial purposes. Printing parts for your own personal or business use is permitted. Selling the files, printed parts, or using them to build competing products is not.

!!! warning "Disclaimer"
    These files are provided as-is. Modifications to the model, print settings or orientation may affect fit and function and are at your own risk. See our [Terms of Use](https://filametric.com/terms-of-use){:target="_blank"} for more information.

---

## Downloads

- [:material-download: Heating Unit Baseplate (.3mf)](../downloads/Filametric_Heating_Unit_Baseplate_3MF.3mf)
- [:material-download: Heating Unit Baseplate (.step)](../downloads/Filametric_Heating_Unit_Baseplate_STEP.step)

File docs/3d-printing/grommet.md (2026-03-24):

---
comments: true
---
# Grommet

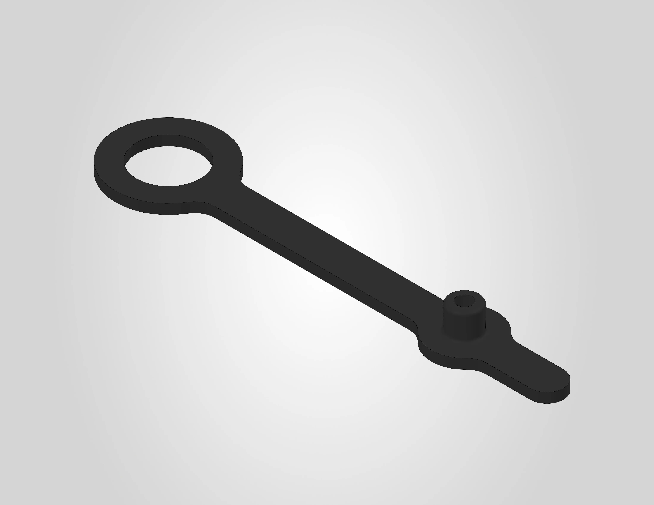
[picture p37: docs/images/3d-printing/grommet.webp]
Grommet


The grommet is used to seal unused openings on the drybox container. It is printed in flexible TPU to ensure a snug, airtight fit. The 3MF file is pre-configured for a Bambu Lab H2S printer with the settings below already applied. If you are using a different printer, use the settings below as a reference.

A STEP file is also included for users who wish to slice the model independently or adapt it for a different printer.

| | |
|---|---|
| **Dimensions** | 16 x 67.9 x 5.5 mm |
| **Estimated print time** | ~4 minutes |
| **Recommended material** | TPU 95A |

---

## Before you print

!!! warning "Pre-drying is required"
    TPU is sensitive to moisture and **must** be dried before printing. Follow the filament manufacturer's drying instructions.

---

## Filament settings

The .3mf file uses the default Bambu Lab TPU 95A HF profile. No parameters were changed from the default profile.

It is recommended to use **TPU 95A**, as this part has been tested and validated with Bambu Lab TPU 95A HF. Other TPU brands should work as well, as long as they have a similar shore hardness (95A or close to it).

---

## Workspace settings

The following workspace settings were changed from the default settings:

| Setting | Value |
|---|---|
| Nozzle | **0.4 mm** |
| Layer height | **0.2 mm** |
| Build plate | **Engineering plate** |
| Sparse infill pattern | **Rectilinear** |
| Supports | **disabled** |

!!! note "No adhesives needed"
    No glue or other adhesives are required on the engineering plate for this print.

The image below shows the sliced result:

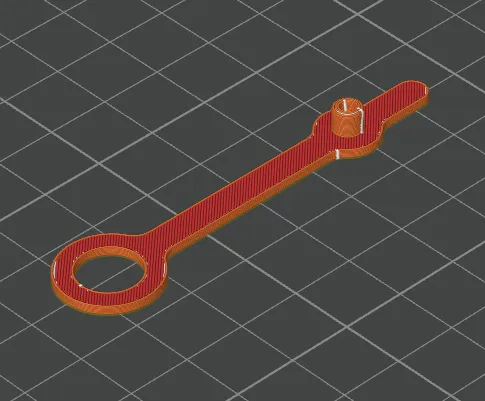
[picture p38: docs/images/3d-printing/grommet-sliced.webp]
Sliced result


---

## License & Disclaimer

!!! note "CC BY-NC 4.0"
    All files on this page are licensed under [CC BY-NC 4.0](https://creativecommons.org/licenses/by-nc/4.0/){:target="_blank"}. You are free to download, print, share and adapt them, as long as you credit Filametric and do not use them for commercial purposes. Printing parts for your own personal or business use is permitted. Selling the files, printed parts, or using them to build competing products is not.

!!! warning "Disclaimer"
    These files are provided as-is. Modifications to the model, print settings or orientation may affect fit and function and are at your own risk. See our [Terms of Use](https://filametric.com/terms-of-use){:target="_blank"} for more information.

---

## Downloads

- [:material-download: Grommet (.3mf)](../downloads/Filametric_Grommet_3MF.3mf)
- [:material-download: Grommet (.step)](../downloads/Filametric_Grommet_STEP.step)

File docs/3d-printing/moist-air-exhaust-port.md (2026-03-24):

---
comments: true
---
# Moist air exhaust port

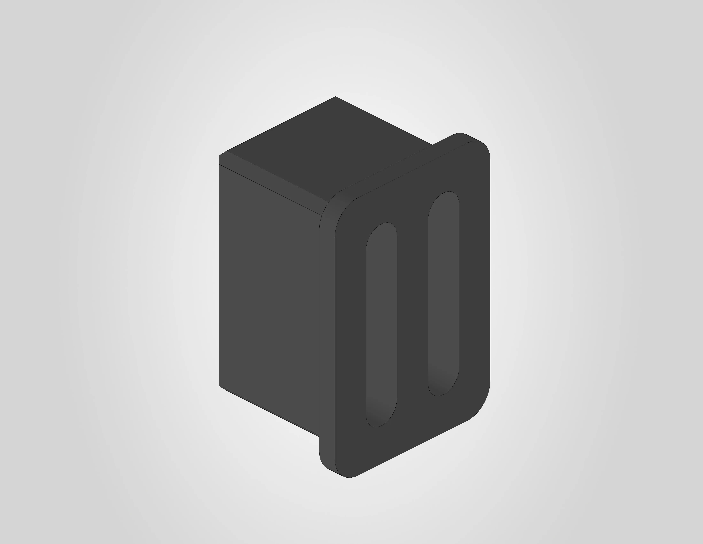
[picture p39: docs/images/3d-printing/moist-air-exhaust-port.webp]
Moist air exhaust port


The moist air exhaust port is a small part that fits into the DryBase housing. The 3MF file is pre-configured for a Bambu Lab H2S printer with the settings below already applied. If you are using a different printer, use the settings below as a reference.

A STEP file is also included for users who wish to slice the model independently or adapt it for a different printer.

| | |
|---|---|
| **Dimensions** | 10 x 14.6 x 9 mm |
| **Estimated print time** | ~7 minutes |
| **Recommended material** | ABS |

---

## Before you print

!!! warning "ABS requires proper ventilation"
    ABS produces fumes during printing. Make sure your printer is enclosed and the room is well ventilated.

!!! warning "Pre-drying is required"
    ABS is sensitive to moisture and **must** be dried before printing. Follow the filament manufacturer's drying instructions.

---

## Filament settings

The .3mf file uses the generic Bambu Lab ABS profile. No parameters were changed from the default profile.

It is recommended to use **ABS**, as this part has been tested and validated with Bambu Lab ABS. Other ABS brands should work as well.

!!! warning "Other materials"
    Other materials may work, but must have at least the same heat resistance as ABS, as these parts are exposed to elevated temperatures during operation. Alternative materials have not been officially tested or validated. Using them is at your own risk and may affect dimensional accuracy and fit.

---

## Workspace settings

The following workspace settings were changed from the default settings:

| Setting | Value |
|---|---|
| Nozzle | **0.4 mm** |
| Layer height | **0.2 mm** |
| Build plate | **Engineering plate** |
| Sparse infill pattern | **Gyroid** |
| Supports | **disabled** |

!!! note "No adhesives needed"
    No glue or other adhesives are required on the engineering plate for this print.

The image below shows the sliced result:

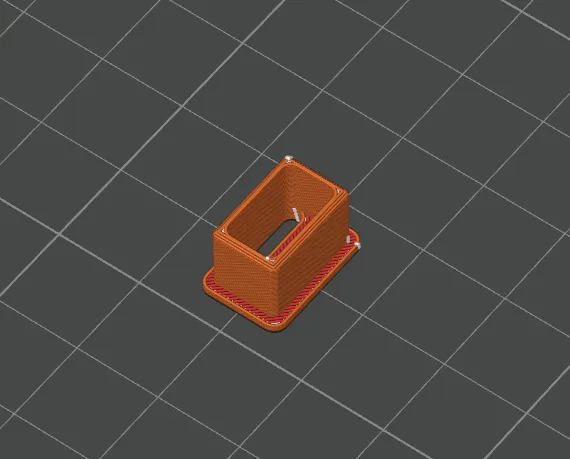
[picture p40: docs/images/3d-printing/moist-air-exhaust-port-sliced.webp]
Sliced result


---

## License & Disclaimer

!!! note "CC BY-NC 4.0"
    All files on this page are licensed under [CC BY-NC 4.0](https://creativecommons.org/licenses/by-nc/4.0/){:target="_blank"}. You are free to download, print, share and adapt them, as long as you credit Filametric and do not use them for commercial purposes. Printing parts for your own personal or business use is permitted. Selling the files, printed parts, or using them to build competing products is not.

!!! warning "Disclaimer"
    These files are provided as-is. Modifications to the model, print settings or orientation may affect fit and function and are at your own risk. See our [Terms of Use](https://filametric.com/terms-of-use){:target="_blank"} for more information.

---

## Downloads

- [:material-download: Moist Air Exhaust Port (.3mf)](../downloads/Filametric_Moist_Air_Exhaust_Port_3MF.3mf)
- [:material-download: Moist Air Exhaust Port (.step)](../downloads/Filametric_Moist_Air_Exhaust_Port_STEP.step)

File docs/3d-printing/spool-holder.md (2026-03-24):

---
comments: true
---
# Spool holder

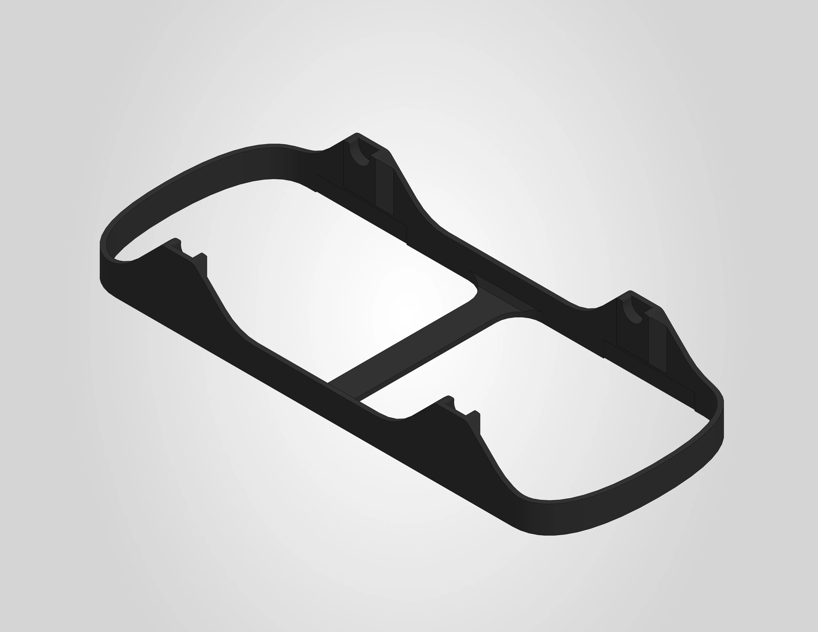
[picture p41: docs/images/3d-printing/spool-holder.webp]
Spool holder


The spool holder sits inside the drybox container lid and holds your filament spool in place. The 3MF file is pre-configured for a Bambu Lab H2S printer with the settings below already applied. If you are using a different printer, use the settings below as a reference.

A STEP file is also included for users who wish to slice the model independently or adapt it for a different printer.

| | |
|---|---|
| **Dimensions** | 86 x 216.5 x 30 mm |
| **Estimated print time** | ~44 minutes |
| **Recommended material** | ABS |

---

## Before you print

!!! warning "ABS requires proper ventilation"
    ABS produces fumes during printing. Make sure your printer is enclosed and the room is well ventilated.

!!! warning "Pre-drying is required"
    ABS is sensitive to moisture and **must** be dried before printing. Follow the filament manufacturer's drying instructions.

---

## Filament settings

The .3mf file uses the generic Bambu Lab ABS profile. No parameters were changed from the default profile.

It is recommended to use **ABS**, as this part has been tested and validated with Bambu Lab ABS. Other ABS brands should work as well.

!!! warning "Other materials"
    Other materials may work, but must have at least the same heat resistance as ABS, as these parts are exposed to elevated temperatures during operation. Alternative materials have not been officially tested or validated. Using them is at your own risk and may affect dimensional accuracy and fit.

---

## Workspace settings

The following workspace settings were changed from the default settings:

| Setting | Value |
|---|---|
| Nozzle | **0.4 mm** |
| Layer height | **0.2 mm** |
| Build plate | **Engineering plate** |
| Sparse infill pattern | **Gyroid** |
| Supports | **disabled** |

!!! note "No adhesives needed"
    No glue or other adhesives are required on the engineering plate for this print.

The image below shows the sliced result:

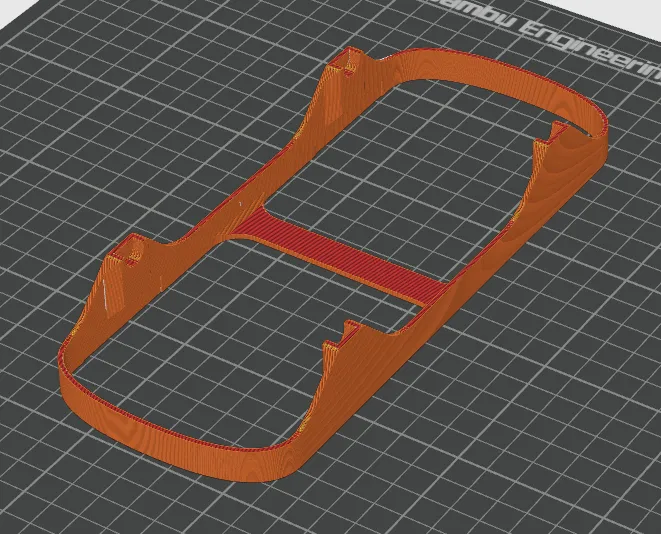
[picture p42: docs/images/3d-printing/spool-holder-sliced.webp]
Sliced result


---

## License & Disclaimer

!!! note "CC BY-NC 4.0"
    All files on this page are licensed under [CC BY-NC 4.0](https://creativecommons.org/licenses/by-nc/4.0/){:target="_blank"}. You are free to download, print, share and adapt them, as long as you credit Filametric and do not use them for commercial purposes. Printing parts for your own personal or business use is permitted. Selling the files, printed parts, or using them to build competing products is not.

!!! warning "Disclaimer"
    These files are provided as-is. Modifications to the model, print settings or orientation may affect fit and function and are at your own risk. See our [Terms of Use](https://filametric.com/terms-of-use){:target="_blank"} for more information.

---

## Downloads

- [:material-download: Spool Holder (.3mf)](../downloads/Filametric_Spool_Holder_3MF.3mf)
- [:material-download: Spool Holder (.step)](../downloads/Filametric_Spool_Holder_STEP.step)

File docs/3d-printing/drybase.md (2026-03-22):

# DryBase

Select a component below to view its printing guide and download the files.

<div class="print-grid" markdown>

<a class="print-card" href="../../3d-printing/housing/">
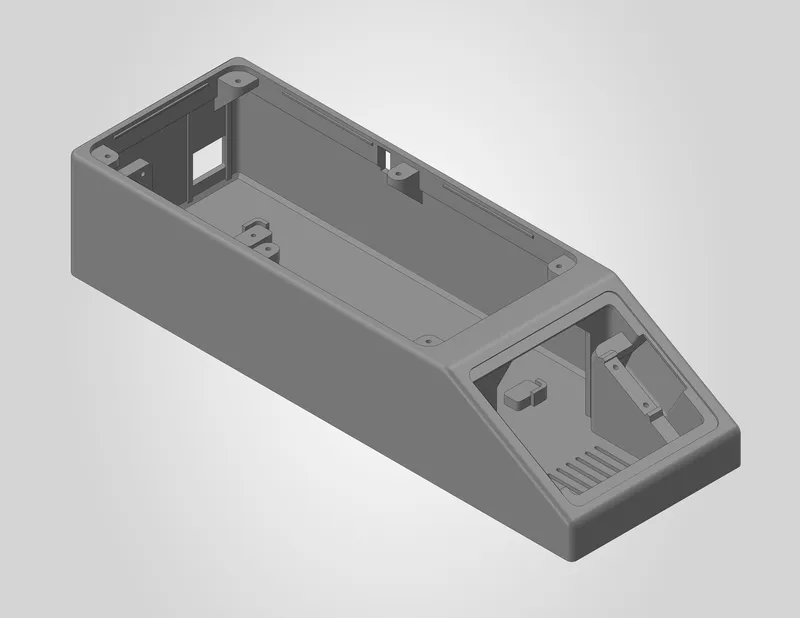
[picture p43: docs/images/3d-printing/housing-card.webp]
Housing
  
  <span>Housing</span>
</a>

<a class="print-card" href="../../3d-printing/moist-air-exhaust-port/">
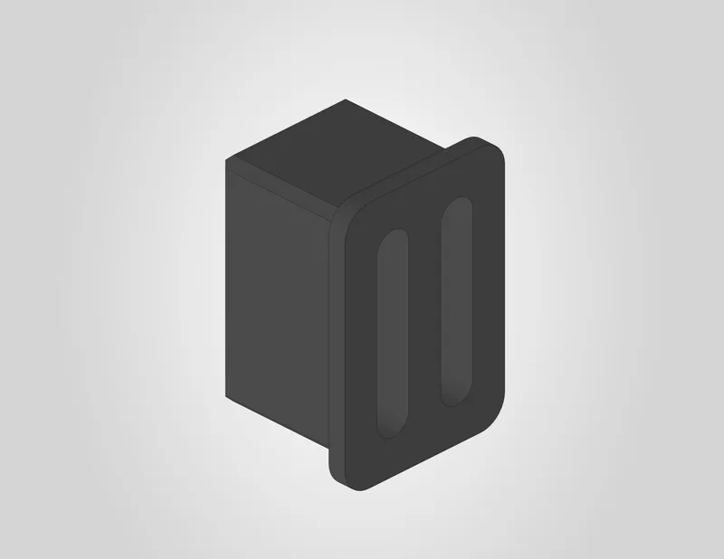
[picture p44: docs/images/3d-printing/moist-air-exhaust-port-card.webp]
Moist air exhaust port
  
  <span>Moist air exhaust port</span>
</a>

<a class="print-card" href="../../3d-printing/heating-unit-baseplate/">
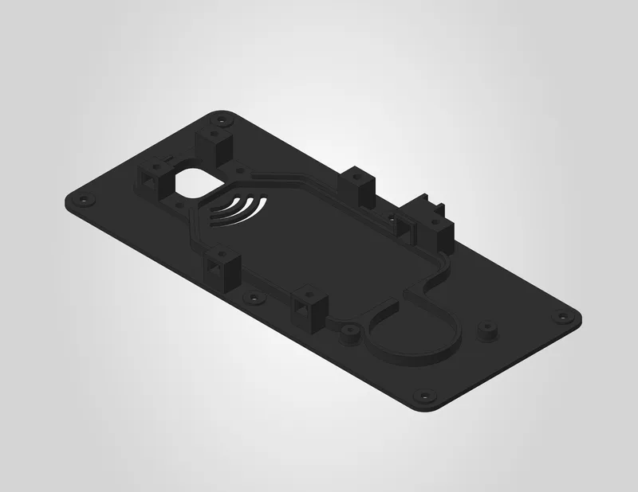
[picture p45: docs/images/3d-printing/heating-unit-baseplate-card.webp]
Heating unit baseplate
  
  <span>Heating unit baseplate</span>
</a>

<a class="print-card" href="../../3d-printing/heating-element-top-cover/">
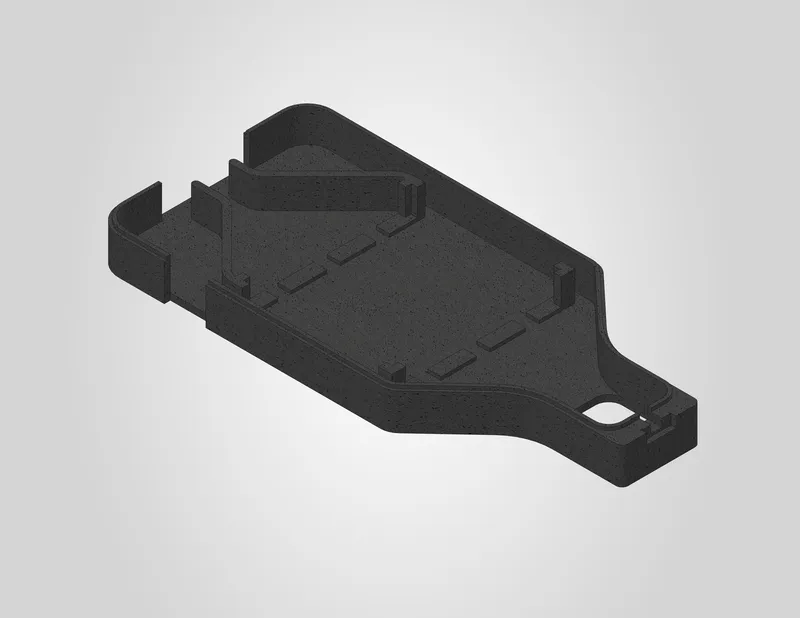
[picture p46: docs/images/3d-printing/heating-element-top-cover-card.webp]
Heating element top cover
  
  <span>Heating element top cover</span>
</a>

<a class="print-card" href="../../3d-printing/heating-element-bottom-cover/">
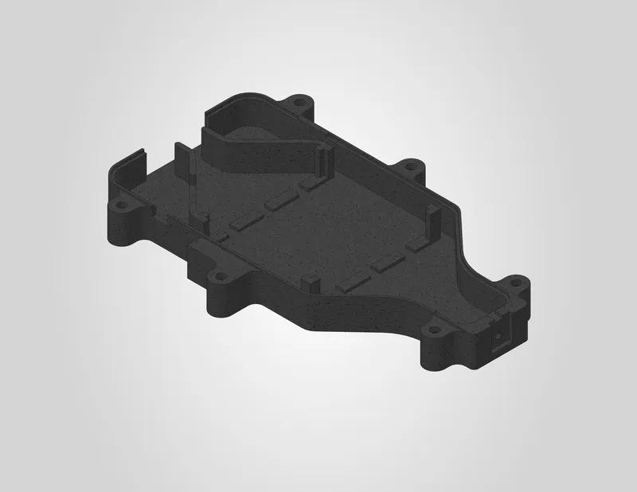
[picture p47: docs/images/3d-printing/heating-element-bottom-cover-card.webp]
Heating element bottom cover
  
  <span>Heating element bottom cover</span>
</a>

<a class="print-card" href="../../3d-printing/hot-air-exhaust-port/">
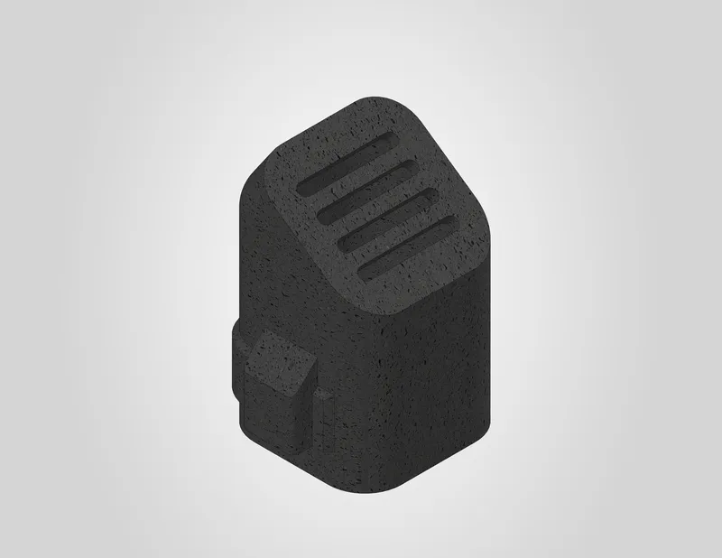
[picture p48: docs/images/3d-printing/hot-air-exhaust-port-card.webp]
Hot air exhaust port
  
  <span>Hot air exhaust port</span>
</a>

<a class="print-card" href="../../3d-printing/container-adapter/">
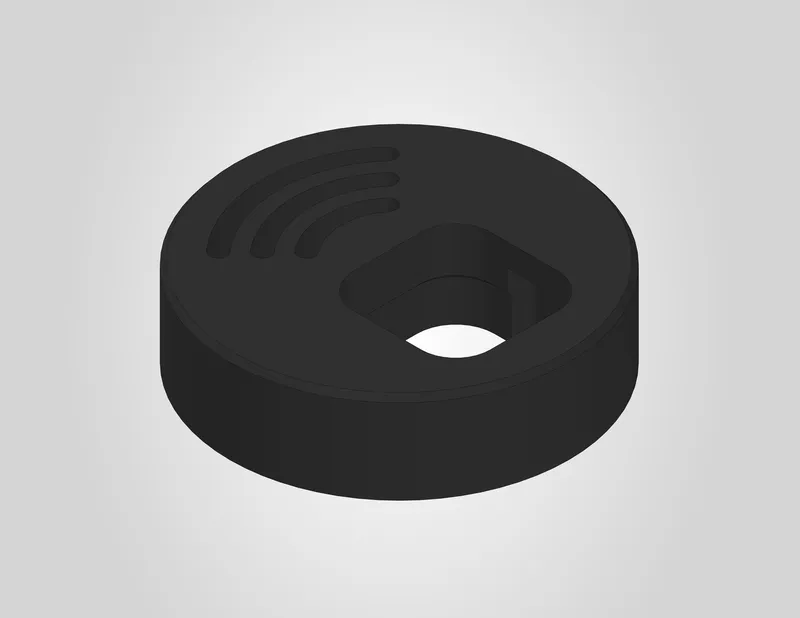
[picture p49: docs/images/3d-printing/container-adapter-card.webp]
Container adapter
  
  <span>Container adapter</span>
</a>

</div>

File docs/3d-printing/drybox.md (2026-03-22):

# Drybox

Select a component below to view its printing guide and download the files.

<div class="print-grid" markdown>

<a class="print-card" href="../../3d-printing/spool-holder/">
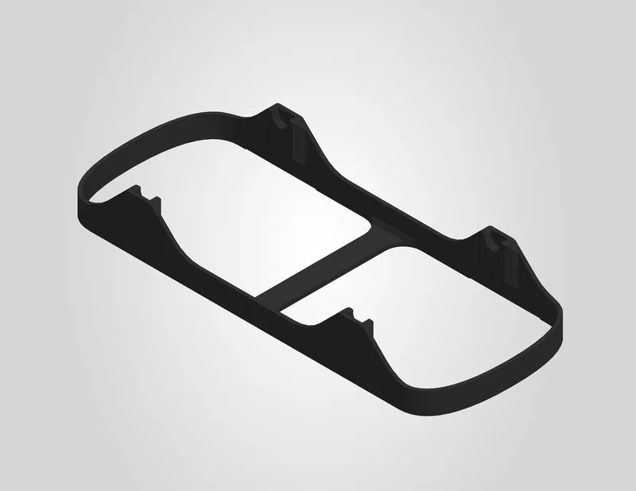
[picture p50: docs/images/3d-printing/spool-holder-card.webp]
Spool holder
  
  <span>Spool holder</span>
</a>

<a class="print-card" href="../../3d-printing/closing-fastener/">
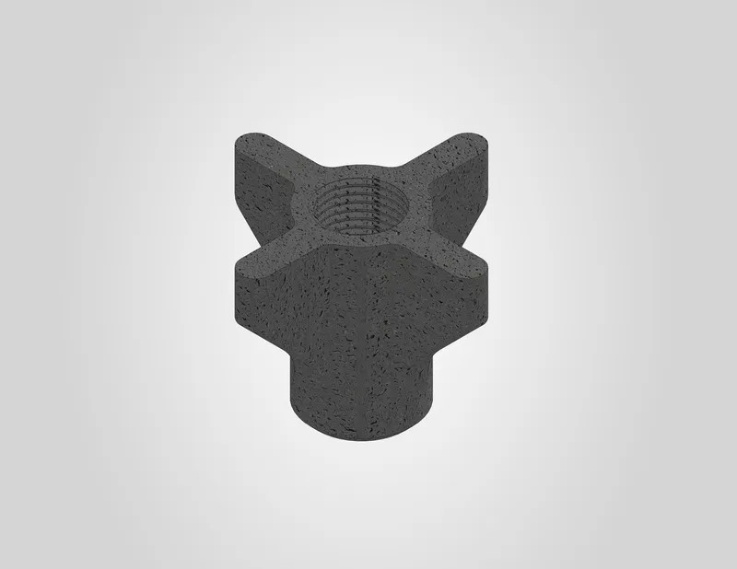
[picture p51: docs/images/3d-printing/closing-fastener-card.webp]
Closing fastener
  
  <span>Closing fastener</span>
</a>

<a class="print-card" href="../../3d-printing/grommet/">
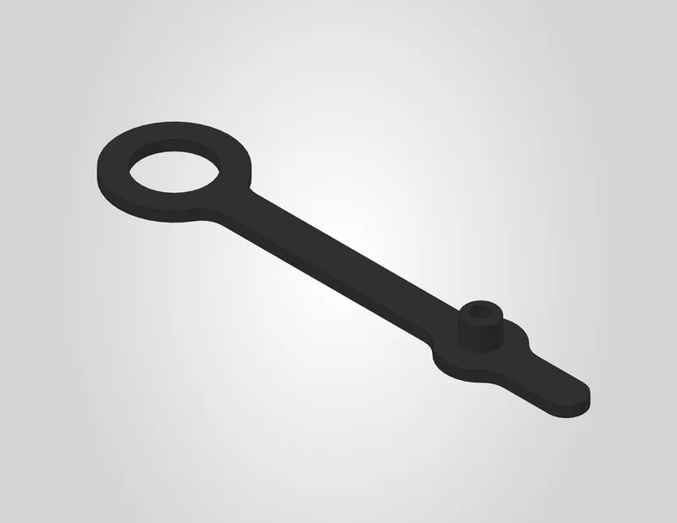
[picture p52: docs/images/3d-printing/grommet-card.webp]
Grommet
  
  <span>Grommet</span>
</a>

</div>

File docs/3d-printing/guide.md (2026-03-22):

# 3D Printing

Select a product below to view its printable components.

<div class="print-grid" markdown>

<a class="print-card" href="../../3d-printing/drybase/">
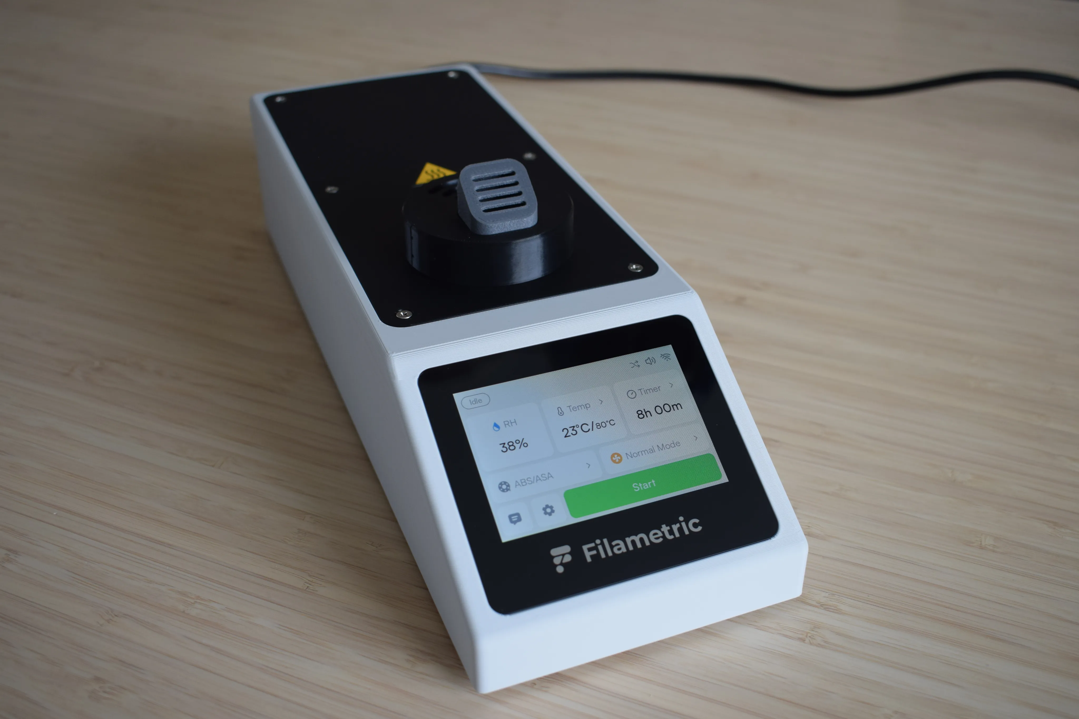
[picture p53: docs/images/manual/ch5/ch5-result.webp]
DryBase
  
  <span>DryBase</span>
</a>

<a class="print-card" href="../../3d-printing/drybox/">
  Drybox
  <span>Drybox</span>
</a>

</div>

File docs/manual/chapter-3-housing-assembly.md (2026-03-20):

---
comments: true
---
[:octicons-arrow-left-24: Chapter 2: Preparing the housing](chapter-2-preparing-housing.md){ .md-button }

# Chapter 3: Housing assembly

In this chapter you will assemble the housing, installing the power supply unit (PSU), exhaust fan, circuit boards, and display. This chapter takes roughly 60-90 minutes to complete. The result will look like the image below.

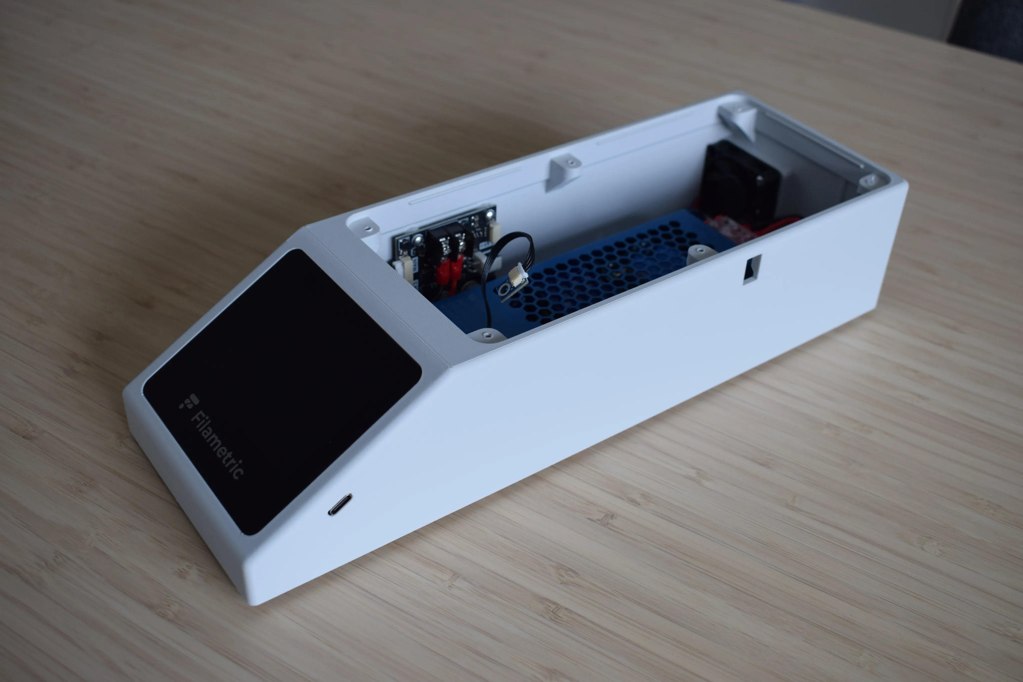
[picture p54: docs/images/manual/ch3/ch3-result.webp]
Chapter 3 result


## Step 1: Installing the C6 inlet

**You will need:**

- DryBase housing
- C6 inlet *(from the Cables bag)*
- Microfiber cloth

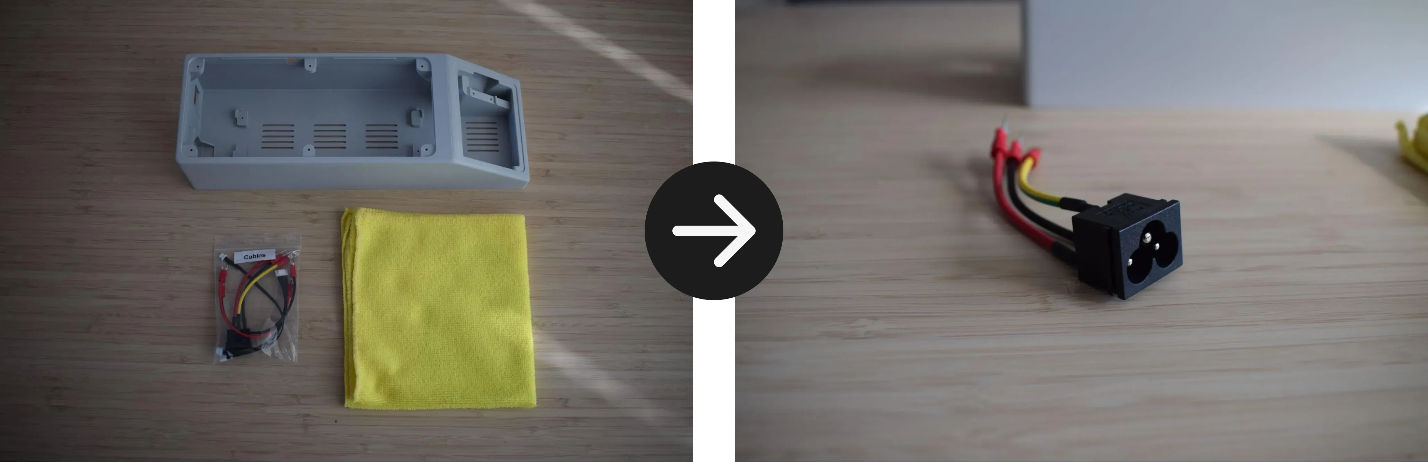
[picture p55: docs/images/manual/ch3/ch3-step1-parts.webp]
Step 1 parts


**a.** Locate the power socket opening at the back of the housing and insert the C6 inlet, aligning it flush with the left edge. Refer to the images below for the correct orientation.

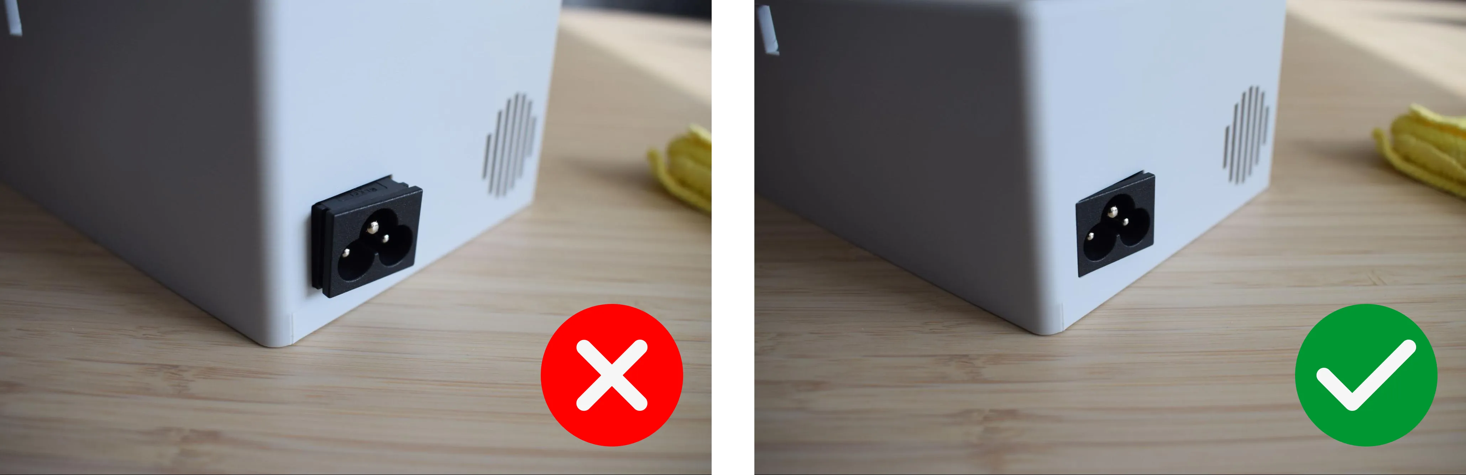
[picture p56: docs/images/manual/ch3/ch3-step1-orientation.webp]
Inlet orientation


**b.** Stand the housing upright on the microfiber cloth with the back panel facing down. Then, apply firm downward pressure from the top until you hear and feel a clear snap. This confirms the inlet is seated.

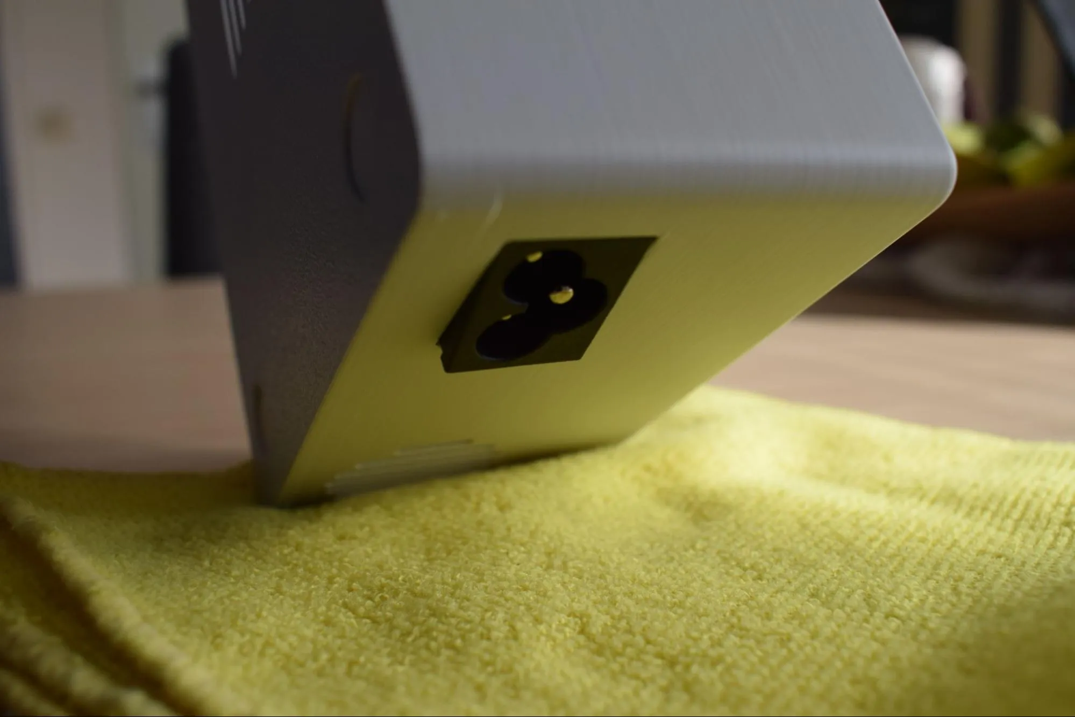
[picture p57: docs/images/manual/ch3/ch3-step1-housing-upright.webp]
Housing upright on cloth


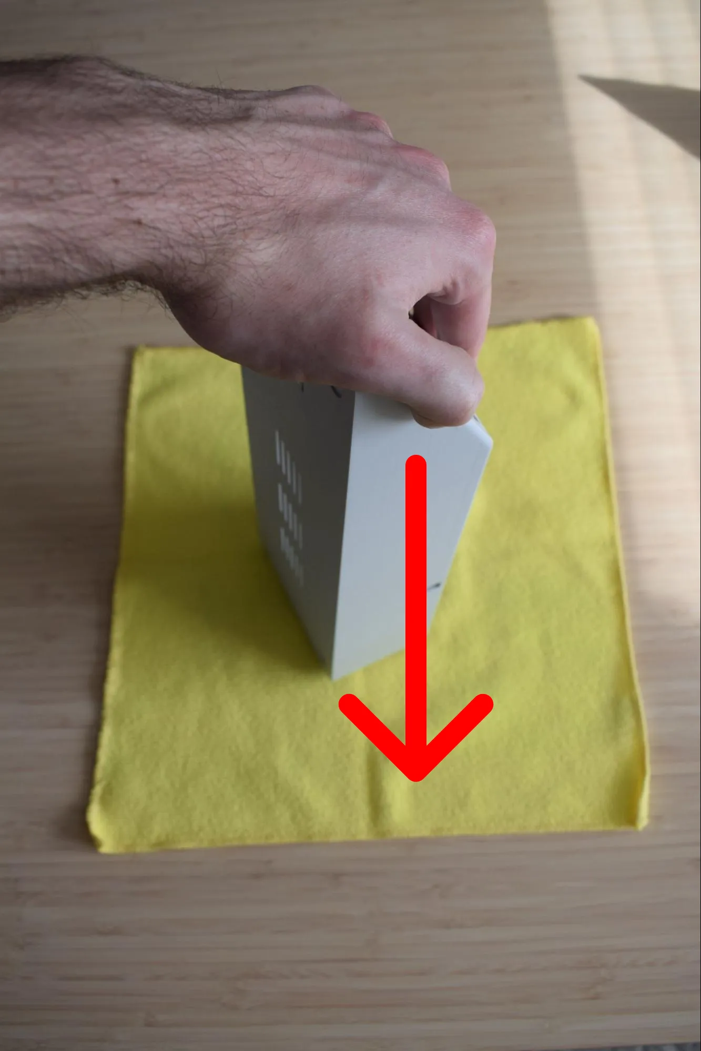
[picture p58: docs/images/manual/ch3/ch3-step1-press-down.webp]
Press down firmly


The images below show how the correctly installed inlet looks from the outside and the inside of the housing.

!!! warning "Check the snap"
    If you did not hear or feel a clear snap, the inlet may not be fully seated. Remove it and try again. A loose inlet can cause connection issues later.

Result outside

Result inside

---

## Step 2: Installing the exhaust fan

**You will need:**

- Housing assembly *(from the previous step)*
- Exhaust fan *(from the Exhaust fan bag)*
- 1x 2.9 x 16mm round-headed screw *(DIN7981; from the Screws / Fasteners bag)*
- Microfiber cloth
- Phillips screwdriver

Step 2 parts

**a.** Before installing the fan, route its cable so it runs flat along the side of the fan housing, not sticking out from the front. The cable should be tucked neatly against the fan body, not protruding outward.

Cable routing

**b.** Press the fan into the dedicated pocket at the back of the housing. Inserting it at a slight angle first, then pushing it flat, makes this easier. **Make sure the fan sticker is facing outward, towards the back of the housing.**

Insert fan into pocket

Once seated, ensure the cables are routed along the inside wall of the housing and are not pinched between the fan and the housing.

Cable routing overview

Cable routing close-up

**c.** Secure the fan using the 2.9 x 16mm round-headed screw and your Phillips screwdriver.

!!! warning "Do not overtighten"
    The housing is 3D-printed and the material can crack or strip if too much force is applied. Stop as soon as the fan sits firmly in place.

Secure fan with screw

---

## Step 3: Connecting the power cables to the PSU

**You will need:**

- Power supply unit (PSU)
- 2x power cables with fork terminals (red & black) *(from the Cables bag)*
- Microfiber cloth
- Phillips screwdriver

Step 3 parts

**a.** Remove the PSU from its packaging and inspect it for any visible damage before proceeding.

PSU inspection

**b.** Locate the output terminal block on the PSU. The terminals are labeled from left to right: **V+, V+, V-, V-**. You will be connecting to terminals 1 and 3, as indicated by the red outlines in the image below. Loosen both terminal screws just enough to insert the fork terminals.

Terminal block with positions 1 and 3 marked

Loosening the terminal screws

**c.** Insert the cables into the terminal block:

- Red wire to the first V+ terminal (position 1)
- Black wire to the first V- terminal (position 3)

!!! warning "Polarity is critical"
    Reversing the red and black wires will damage the DryBase electronics. Double-check before tightening.

**d.** Tighten both terminal screws securely. Give each wire a gentle tug to confirm it is properly seated and cannot be pulled out.

Tightening the terminal screws

**e.** Confirm that the final result matches the image below: the red wire seated in the first V+ terminal and the black wire in the first V- terminal, with both screws tightened and the remaining terminals left empty.

Final result

---

## Step 4: Connecting the PSU to the power board

**You will need:**

- Power supply + attached cables *(from the previous step)*
- Power board *(from the Power board bag)*
- Microfiber cloth
- Phillips screwdriver

**a.** Unpack the power board from its anti-static bag and place it on the microfiber cloth.

Unpack power board

**b.** Locate the two screw terminals on the power board, labeled **GND** and **24V**. Loosen both terminal screws using your Phillips screwdriver, just enough to insert the fork terminals.

GND and 24V terminals

**c.** Insert the **red wire** into the **24V-labeled terminal**. Make sure the wire runs downward as shown in the image below.

Red wire into 24V terminal

**d.** Insert the **black wire** into the **GND-labeled terminal**. Make sure the wire runs downward in the same direction as the red wire.

Black wire into GND terminal

!!! warning "Polarity is critical"
    Red must go to 24V and black to GND. Reversing the wires will damage the power board and other electronics. Double-check before tightening.

**e.** Tighten both terminal screws securely and give each wire a gentle tug to confirm it is properly seated. Confirm that the final result matches the image below.

Final result

---

## Step 5: Installing the PSU into the housing

**You will need:**

- Housing assembly *(from a previous step)*
- Power supply + attached cables & power board *(from the previous step)*
- 2x 2.9 x 6.5mm round-headed screws *(DIN7981; from the Screws / Fasteners bag)*
- Microfiber cloth
- Phillips screwdriver

**a.** Place the housing on the microfiber cloth with the open side facing up. Drive a 2.9 x 6.5mm round-headed screw into the front mounting hole as shown in the image below, leaving 2-3mm of spacing between the screw head and the housing. This acts as a rail to slide the PSU under.

Front screw as rail

**b.** Hold the power board in your left hand and the PSU in your right hand. Tilt the PSU at a slight angle and slide the front edge underneath the partially tightened screw, as shown in the images below.

Slide PSU under screw

**c.** Once the front of the PSU is seated under the screw, lower the back of the PSU down into the housing until it sits flat, as shown in the image below.

Lower PSU into housing

**d.** Tighten the front screw to secure the PSU in place.

!!! warning "Do not overtighten"
    The housing is 3D-printed and the material can crack or strip if too much force is applied. Stop as soon as the PSU sits firmly in place.

Tighten front screw

**e.** Drive the second 2.9 x 6.5mm round-headed screw into the back mounting hole to fully secure the PSU.

Back screw

**f.** Rest the power board in the housing as shown in the image below. It will be secured in a later step.

Power board resting in housing

---

## Step 6: Connecting the C6 inlet and exhaust fan

**You will need:**

- Housing assembly *(from the previous step)*
- Microfiber cloth
- Phillips screwdriver

**a.** Locate the AC input terminal block on the back side of the PSU (these are the terminals not yet connected). Lift the transparent plastic cover to access them, then loosen all three terminal screws to allow the fork terminals to fit in.

Open cover and loosen screws

**b.** Insert the three wires from the power socket into the terminal block in the correct order.

- Yellow/green wire to the left terminal (⏚ - Ground)
- Red wire to the middle terminal (L - Live)
- Black wire to the right terminal (N - Neutral)

!!! warning "Safety warning"
    This terminal block connects directly to mains voltage. Double check all three wire positions before tightening. Incorrect wiring can cause permanent damage or create a safety hazard.

Correct wire placement

**c.** Tighten all three terminal screws securely, then close the transparent plastic cover. Give each wire a gentle tug to confirm the fork terminals are fully secured and cannot be pulled loose.

Tighten terminal screws

**d.** Verify that the wiring matches the image below. Check both the wire routing and polarity from the front view before continuing.

Verify wiring from front

**e.** Connect the exhaust fan cable to the connector labeled **FAN 1** on the power board. A clear click should be heard and felt when the connector is fully seated. Give the cable a gentle tug to confirm it is secure. Place the power board back in its position in the housing. It will be fully secured in a later step.

Fan connector to FAN 1

---

## Step 7: Placing the rubber feet

**You will need:**

- Housing assembly *(from the previous step)*
- 4x rubber feet *(from the Adhesives bag)*

**a.** Remove the strip of 4 rubber feet from the Adhesives bag.

Rubber feet parts

**b.** Press one rubber foot into each of the four corner cavities at the bottom of the housing.

!!! note "Be mindful of the power board"
    The power board is not yet secured to the housing and can shift during handling.

Rubber foot installed

---

## Step 8: Connecting the display and Main & Sensor board

**You will need:**

- Housing assembly *(from the previous step)*
- Main & Sensor board *(from the Main & Sensor board bag)*
- Main & Sensor board cables *(from the Cables bag)*
- Display *(from the Display bag)*
- Microfiber cloth

Step 8 parts

**a.** Remove both cables and the Main & Sensor board from their bags. Place them on the microfiber cloth as shown in the image below.

Unpack components

**b.** Connect both cables to the Main board. A clear click should be heard when each connector is fully seated. Give each cable a gentle tug to confirm it is secure.

Cables connected to Main board

**c.** Connect the Sensor board to the other end of the 4-wire cable. This connector slides in without a click (it is seated correctly when it sits flush as shown in the image below).

Sensor board connected

Confirm that the assembly matches the image below before continuing.

Assembly check

**d.** Remove the display from its bag.

!!! warning "Handle with care"
    Only touch the FPC cables at their middle and never at the exposed pads or connectors. Oil and pressure from your fingers can damage the contacts.

How to handle the display

**e.** Remove the red foam protection from the display and place the display face-down on the microfiber cloth, as shown in the image below.

Display face-down

**f.** On the Main board, locate both FPC connectors and open them by gently lifting the locking tab, as shown in the images below. Do this carefully, as the tabs are fragile.

FPC connectors

**g.** Hold the Main board in your left hand and the small FPC touch cable in your right. Refer to the image below to identify the correct cable and connector.

Touch cable identification

**h.** Gently slide the cable into the connector until it is fully seated. The black edge of the FPC touch cable should extend ever so slightly beyond the connector, as indicated by the red arrow in the image on the right below. Once correctly positioned, close the locking tab by pressing it down gently until it clicks into place. **Do not force it.**

Touch cable connection

**i.** Flip the Main board over so the FPC display connector is now facing up, and position it alongside the display as shown in the image below.

Flip and position

**j.** Hold the large FPC display cable in your left hand and the Main board in your right, as shown in the image below.

Display cable positioning

**k.** Slide the cable into the wide FPC connector, aligning the white line on the cable with the white line marking on the Main board. Once correctly positioned, close the locking tab by pressing it down gently to secure the connection.

Display cable connected

---

## Step 9: Installing the display assembly into the housing

**You will need:**

- Housing assembly *(from a previous step)*
- Display assembly *(from the previous step)*
- 2x 2.9 x 6.5mm round-headed screws *(DIN7981; from the Screws / Fasteners bag)*
- Microfiber cloth
- Phillips screwdriver

Step 9 parts

**a.** Remove the protective film from the self-adhesive tape on the back of the display, as shown in the image below.

Peel protective film

**b.** Hold the display in your left hand and the Main board in your right. Pass both cables through the front opening of the housing, as shown in the image below.

!!! note "Keep the display cables straight"
    The FPC cables connecting the display to the Main board are fragile. Keep them as straight as possible at all times to avoid damage to the cables or the FPC connectors on the boards. Do not bend, fold or crease them.

Hold display through opening

**c.** While still holding the display with your left hand, insert the Main board into the housing at an angle. Align the top edge of the board flush with the top edge of the housing, as indicated by the top red arrow in the image below. At the same time, align the USB-C connector of the board with its dedicated slot in the housing, as indicated by the bottom red arrow.

Insert board into housing

**d.** Once everything is correctly aligned, apply light pressure with your finger on the bottom of the board as indicated by the arrow in the image below, until it snaps into place. A clear click should be heard when it is fully seated.

Snap board into place

**e.** Confirm that the Main board is flush with the housing and that the USB-C port is correctly seated in its slot. Then, using your Phillips screwdriver, secure the Main board with both 2.9 x 6.5mm round-headed screws as shown in the image below. Continue holding the display in place with your left hand while tightening.

!!! warning "Do not overtighten"
    The housing is 3D-printed and the material can crack or strip if too much force is applied. Stop as soon as the Main board sits firmly in place.

Screw board in place

The image below shows how the assembly should look after both screws are tightened.

Screws done

**f.** Flip the display over so it faces up, aligning its left edge flush with the left side of the housing, as shown in the image below.

Flip display

**g.** Gently press along all four sides of the display (left, right, top, and bottom) to firmly bond the double-sided tape to the housing, as shown in the images below.

Press display edges

**h.** Confirm that the display sits flush with the housing on all sides and that the USB-C port is correctly accessible through the housing slot, as shown in the images below.

USB-C port check

Final result

---

## Step 10: Connecting and securing the Power board

**You will need:**

- Housing assembly *(from a previous step)*
- 2x 2.9 x 6.5mm round-headed screws *(DIN7981; from the Screws / Fasteners bag)*
- Phillips screwdriver

**a.** Locate the 8-pin cable coming from the Main board and insert it into the connector labeled **'MAIN'** on the Power board. A clear click should be heard when fully seated. Give the cable a gentle tug to confirm it is secure.

Main cable connection

**b.** Insert the Power board into the dedicated slot in the housing at a slight angle, as indicated by the red arrow in the image below.

!!! warning "Check your cables"
    Before pressing it into place, make sure no cables are running behind the board. Trapped cables can cause connection issues or damage components.

Insert power board

**c.** Once the board is correctly seated, align both mounting holes and secure the Power board using the two 2.9 x 6.5mm round-headed screws. Angling the screwdriver slightly may help reach the holes more easily.

!!! warning "Do not overtighten"
    The housing is 3D-printed and the material can crack or strip if too much force is applied. Stop as soon as the Power board sits firmly in place.

Screw power board

**d.** Confirm that the cables are routed as shown in the images below before continuing.

Cable routing check close-up

Cable routing check overview

---

**Congratulations!** You have completed the housing assembly. The DryBase housing is now fully assembled with all electronics installed and connected. Before continuing to the next chapter, take a moment to verify the following:

- [x] All cables are routed along the inside walls and none are pinched or trapped
- [x] The display sits flush with the housing on all sides
- [x] The USB-C port is accessible through its slot
- [x] The main and power board are each secured with two screws
- [x] The rubber feet are firmly seated in all four corners

In the next chapter, you will assemble the **heating unit**.

Completed housing assembly

---

[:octicons-arrow-right-24: Chapter 4: Heating unit assembly](chapter-4-heating-unit-assembly.md){ .md-button .md-button--primary }

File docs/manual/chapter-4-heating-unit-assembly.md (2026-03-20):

---
comments: true
---
[:octicons-arrow-left-24: Chapter 3: Housing assembly](chapter-3-housing-assembly.md){ .md-button }

# Chapter 4: Heating unit assembly

In this chapter you will assemble the heating unit, the core component responsible for generating and distributing heat inside the DryBase. This chapter takes roughly 45-60 minutes to complete. This sub-assembly will be connected to the housing in Chapter 5.

!!! note "Did you know?"
    The dark grey PA6-GF25 components in this chapter were dried at 100°C before and during printing, in a Filametric DryBase of course. This ensures the tightest tolerances, the best possible fit during assembly and a high-quality surface finish.

Chapter 4 result

## Step 1: Preparing the heating element enclosure

**You will need:**

- Heating element *(from the Heating element bag)*
- Heating unit parts *(from the Heating unit parts bag)*
- Microfiber cloth

Step 1 parts

**a.** Remove the heating element and both the top and bottom covers from their bags. Place them on the microfiber cloth. Remove the plastic protective cap from the thermal cut-off as shown in the image below.

Unpack components

Remove protective cap

**b.** Place the heating element into the bottom cover, aligning it with the four corner clips as indicated by the red markers in the image below. Press it down gently until it sits flat and is fully seated in the enclosure.

Insert heating element

Corner clips alignment

**c.** Inspect the thermal cut-off pocket on the side of the enclosure for any obstructions, such as remaining print material and remove if necessary. Slide the thermal cut-off into the pocket as shown in the images below, then push it all the way in using your finger or fingernail until it sits flush with the edge of the enclosure.

!!! warning "Do not use a sharp tool"
    Do not use a sharp tool to push the thermal cut-off into place. A screwdriver or similar object can damage the component. Use your finger or fingernail only.

Slide thermal cut-off

Thermal cut-off check

**d.** Route the cables along the inside of the bottom cover as shown in the images below. Make sure the cables run through the dedicated cable channel and do not cross over the heating element cover.

Cable routing top view

Cable routing side view

**e.** Place the top cover onto the bottom cover. It should close without force.

!!! warning "Do not force the cover"
    If it does not close easily, the cables are likely not routed correctly. Remove the cover, check the cable routing from step d, and try again.

Close top cover

Cover closed

Confirm that the assembly matches the images below before continuing.

Step 1 result

---

## Step 2: Installing the heating element on the baseplate

**You will need:**

- Heating element assembly *(from the previous step)*
- Heating unit baseplate *(from the Heating unit parts bag; the flat black rectangular plate)*
- 6x M3 x 12mm hex bolt *(DIN7984; from the Screws / Fasteners bag)*
- 6x M3 nylon nut *(DIN985; from the Screws / Fasteners bag)*
- Microfiber cloth
- 2mm hex/allen key

Step 2 parts

**a.** Place the baseplate on the microfiber cloth with the nut pockets facing up. Locate all six nut pockets as indicated by the red circles in the image below.

Nut pockets

**b.** Take the 6x M3 nylon nuts and partially insert one into each pocket, with the pointed end facing outward as shown in the images below.

!!! warning "Correct orientation"
    Insert the nuts in the correct orientation before pushing them in fully. Once fully seated, they cannot be removed. Refer to the images below for the correct orientation.

Nut partially inserted

Nut orientation

**c.** Push each nut fully into its pocket using a screwdriver to apply gentle pressure. **Do not use excessive force.** Press until the nut sits flush and the threaded hole is aligned with the bolt hole in the pocket.

!!! warning "Do not scratch or damage the surrounding surface"
    When using the screwdriver to push the nuts in, apply pressure directly onto the nut only.

Push nut with screwdriver

**d.** Verify that all six nuts are fully seated. The nut should not be visible from above, only the threaded hole should remain visible, aligned with the bolt hole, as shown in the images below.

Nut check

**e.** Pick up the heating element assembly and position it onto the baseplate, inserting the left side first as shown in the image below. Once the left side is aligned, lower the right side down until the assembly sits flat on the baseplate.

Place assembly on baseplate

Once released, confirm it sits flat and all mounting holes are aligned, as shown in the image below.

Assembly aligned

**f.** Apply light pressure across the assembly to ensure full contact with the baseplate.

Press down

**g.** Confirm the assembly is correctly seated by checking both connection points as shown in the images below. The heating element enclosure should sit flush against the baseplate with no visible gap on either side.

Seat check

**h.** Using the 2mm hex/allen key, insert and tighten all six M3 x 12mm hex bolts in the order indicated in the image below (1 to 6).

!!! warning "Do not overtighten"
    The nylon nuts are seated in 3D-printed pockets. Excessive force can cause them to spin and lose their grip. The nylon locking insert already provides sufficient holding force. **Tighten until snug and stop.**

Bolt with allen key

Bolt order

**i.** Verify that all sides are flush and no visible gap exists between the top and bottom covers of the heating element enclosure. The images below show a correctly assembled result.

Verify front

Verify side

---

## Step 3: Installing the blower fan, container adapter and exhaust port

**You will need:**

- Heating unit assembly *(from the previous step)*
- Blower fan *(from the Blower fan bag)*
- Container adapter part *(from the Heating unit parts bag; the round black part shown in the top left corner of the image below)*
- Hot air exhaust port *(from the Heating unit parts bag; the dark grey part shown in the top right corner of the image below)*
- 2x 2.9 x 16mm round-headed screw *(DIN7981; from the Screws / Fasteners bag)*
- 2x 3.9 x 25mm round-headed screw *(DIN7981; from the Screws / Fasteners bag)*
- Adhesives bag *(not in the picture below)*
- Microfiber cloth
- Phillips screwdriver

Step 3 parts

**a.** Remove the blower fan from its bag and place it onto the heating unit assembly, aligning it with the two mounting holes on the baseplate as shown in the images below. Make sure the fan label is facing downward, towards the baseplate.

Fan placement

**b.** Using the 2x 3.9 x 25mm round-headed screws and your Phillips screwdriver, secure the blower fan to the baseplate through both mounting holes.

!!! warning "Do not overtighten"
    The baseplate is 3D-printed and the material can crack or strip if too much force is applied. Stop as soon as the blower fan sits firmly in place.

Fan screwing

Confirm the fan is correctly secured as shown in the image below.

Fan secured

**c.** Take the tie wrap from the Blower fan bag and slide it through the dedicated slot on the baseplate from the left side, as shown in the images below.

Tie wrap slot

**d.** Pass the blower fan cable through the tie wrap. Pull the tie wrap tight enough to secure the cable against the baseplate, then trim off the excess with scissors or pliers. Make sure there is no excess slack on the right side of the fan. The goal is to keep the cable routed neatly along the left side.

Cable tie wrap

Refer to the image below for the correct result.

Cable routing correct vs incorrect

**e.** Remove the container adapter and hot air exhaust port from the Heating unit parts bag and place them on the microfiber cloth as shown in the image below.

Adapter and exhaust port parts

**f.** Turn the container adapter upside down so the two holes are facing upward. Insert the hot air exhaust port into the container adapter. Note that there is only one correct orientation in which it will fit. Do not force it.

!!! warning "Do not force the exhaust port into the adapter"
    If it does not slide in easily, rotate it and try again. There is only one orientation in which it fits correctly.

Exhaust port insert

The tabs of the hot air exhaust port should sit fully flush with the bottom face of the container adapter, as shown in the image below. The other side should look like the second image below.

Exhaust flush bottom

Exhaust flush top

**g.** Take the assembled container adapter and place it onto the heating unit assembly, aligning it with the opening in the baseplate. The exhaust port should be facing towards you as shown in the images below.

Adapter placement

**h.** While holding the assembly in place, secure the container adapter using the 2x 2.9 x 16mm round-headed screws, one on each side, using your Phillips screwdriver.

!!! warning "Do not overtighten"
    The container adapter is 3D-printed and the material can crack or strip if too much force is applied. Stop as soon as the container adapter sits firmly in place.

Adapter screwing

**i.** Verify that all parts are correctly aligned with the baseplate and that no visible gaps exist between any of the components. The images below show a correctly assembled result.

Verify side

Verify front

**j.** Remove the 'caution hot surface' sticker from the Adhesives bag and apply it to the top of the baseplate, centered between the container adapter and the edge of the plate, as shown in the image below.

Caution sticker

---

**Congratulations!** You have completed the Heating Unit Assembly.

The heating unit is now fully assembled and ready to be connected to the housing. Before continuing to the next chapter, take a moment to verify the following:

- [x] The blower fan is secured with two screws and the cable is neatly routed with the tie wrap
- [x] The hot air exhaust port sits flush within the container adapter with no visible gap
- [x] The container adapter is secured with two screws and sits flush against the baseplate
- [x] The 'caution hot surface' sticker is applied to the top of the baseplate
- [x] No visible gaps exist between any of the components

In the next chapter, you will connect the heating unit to the housing to complete your **DryBase**.

Chapter 4 result

---

[:octicons-arrow-right-24: Chapter 5: DryBase assembly](chapter-5-drybase-assembly.md){ .md-button .md-button--primary }

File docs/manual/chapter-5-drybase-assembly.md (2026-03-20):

---
comments: true
---
[:octicons-arrow-left-24: Chapter 4: Heating unit assembly](chapter-4-heating-unit-assembly.md){ .md-button }

# Chapter 5: DryBase assembly

In this chapter you will install the heating unit into the housing to complete your DryBase. This is the final assembly step and by the end of this chapter, your DryBase will be fully assembled and ready for use. This chapter takes roughly 30 minutes to complete.

Chapter 5 result

## Step 1: Installing the heating unit into the housing

**You will need:**

- Completed housing assembly *(from Chapter 3)*
- Completed heating unit assembly *(from Chapter 4)*
- Moist air exhaust port *(final part from the Heating unit parts bag)*
- 1x 2.9 x 6.5mm round-headed screw *(DIN7981; from the Screws / Fasteners bag)*
- 6x 2.9 x 9.5mm countersunk screw *(DIN7982; from the Screws / Fasteners bag)*
- Microfiber cloth
- Phillips screwdriver
- C5 1.5m power cord cable *(not shown in the picture below)*

Step 1 parts

**a.** Locate the rectangular cut-out on the right side of the housing. Take the moist air exhaust port and push it into the cut-out as shown in the images below. Make sure the part sits flush with the side of the housing. The orientation does not matter.

Moist air exhaust port installation

**b.** Hold the heating unit with your left hand and connect the heating element cable to the power board, as indicated by the red circle in the image below. An audible click should be heard. Give the cable a small tug to confirm it is properly seated.

Heating element cable overview

Heating element cable connected

**c.** While still holding the heating unit with your left hand, connect the blower fan cable to the power board as indicated by the red circle in the image below. An audible click should be heard. Give the cable a small tug to confirm it is properly seated.

Blower fan cable connected

**d.** Lean the heating unit against the back of the housing as shown in the left image below, keeping the front side upright. Take the sensor board together with its cable and position it at the front of the heating unit, aligning the mounting holes as shown in the right image below.

Sensor board positioning

**e.** Using the 1x 2.9 x 6.5mm round-headed screw and your Phillips screwdriver, secure the sensor board to the heating unit.

!!! warning "Do not overtighten"
    The heating unit cover is 3D-printed and the material can crack or strip if too much force is applied. Stop as soon as the sensor board sits firmly in place.

Sensor board secured

**f.** You are now ready to lower the heating unit into the housing. Before doing so, read through this step completely before proceeding.

!!! warning "Do not force the heating unit down"
    Lower it evenly on all sides simultaneously, keeping the wires clear on the left side and the moist air exhaust port aligned with the cut-out on the right side (when viewing from the front of the DryBase).

Make sure the moist air exhaust port and the heating unit are aligned as shown in the image below.

Alignment before lowering

Verify the following before continuing:

On the right side, ensure the opening on the heating unit is aligned with the moist air exhaust port in the housing and sits flush, as shown in the images below.

Exhaust port flush check

On the left side, make sure no wires are pinched between the housing and the heating unit, as shown in the correct and incorrect images below.

Wires check

Wires correct

Ensure the corners on both the front and back are properly aligned with no debris or cables caught between the heating unit and the housing.

Corners check

The final result should show no visible gap between the heating unit and the housing, as shown in the image below.

No visible gap

**g.** Using your Phillips screwdriver, insert and tighten all six 2.9 x 9.5mm countersunk screws in the order shown in the image below (1 to 6).

!!! warning "Do not overtighten"
    The housing is 3D-printed and the material can crack or strip if too much force is applied. Stop as soon as the heating unit sits firmly in place.

Screw order

Screwing

**h.** Once all screws are secured, confirm that the assembly matches the image below before continuing.

Verification

**i.** Insert the C5 power cord into the inlet on the back of the housing. Make sure it is pushed in fully and sits flush, as shown in the correct and incorrect images below. Connect the other end of the power cord to a wall outlet. The DryBase will power on automatically and the display should light up and show the home screen within a few seconds.

Power cord connection

---

**Congratulations!** You have successfully assembled your DryBase.

Your DryBase is now fully assembled and powered on. The display should light up and show the home screen, as shown in the image below. You are ready to start drying. Before continuing to the next chapter, take a moment to verify the following:

- [x] No visible gap exists between the heating unit and the housing on any side
- [x] The moist air exhaust port is flush with the right side of the housing
- [x] No wires are visible or pinched along the edges
- [x] All six countersunk screws are secured
- [x] The C5 power cord is fully seated and the display powers on

!!! note "Display not turning on?"
    Check that the power cord is fully seated and that the wall outlet is active. If the issue persists, contact us at [support@filametric.com](mailto:support@filametric.com).

DryBase assembled

---

[:octicons-arrow-right-24: Chapter 6: Drybox assembly](chapter-6-drybox-assembly.md){ .md-button .md-button--primary }

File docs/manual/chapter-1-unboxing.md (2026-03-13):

---
comments: true
---
[:octicons-arrow-left-24: Introduction](introduction.md){ .md-button }

# Chapter 1: Unboxing & checking components

Before you begin the assembly, unbox your DryBase kit and verify that all components are present. Lay everything out on a clean, flat surface.

Kit overview

The image above is divided into two sections. The **blue box** on the left shows what you need to provide yourself. The **green box** on the right shows everything included in your kit.

## What you need to provide

- DryBase housing (3D-printed; see the [3D Printing guide](../3d-printing/housing.md) for material requirements)
- Phillips screwdriver
- 2mm hex/allen key
- Microfiber cloth (for handling components)

## What's included in your kit

From left to right, top to bottom:

- 150W Power Supply Unit (PSU)
- C5 1.5m power cord (region-specific)
- Heating unit parts (bag)
- Display (bag)
- Cables (bag)
- Drybox parts (bag)
- Main & sensor board (bag)
- Power board (bag)
- Heating element (bag)
- Exhaust fan (bag)
- Blower fan (bag)
- Adhesives (bag)
- Screws / fasteners (bag)
- Spares (bag)

!!! note "Missing or damaged parts?"
    Contact us at [support@filametric.com](mailto:support@filametric.com) with your order number and a photo of the issue before proceeding.

---

[:octicons-arrow-right-24: Chapter 2: Preparing the housing](chapter-2-preparing-housing.md){ .md-button .md-button--primary }

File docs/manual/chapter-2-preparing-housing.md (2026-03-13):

---
comments: true
---
[:octicons-arrow-left-24: Chapter 1: Unboxing](chapter-1-unboxing.md){ .md-button }

# Chapter 2: Preparing the DryBase housing

After printing your DryBase housing, it needs to be cleaned up before assembly. This chapter covers removing all support material.

## Step 1: Removing top support material

Locate and remove the tree support material from the inside of the housing. There are four locations, indicated by the red circles in the image below.

Top support locations

Use your hands or a pair of pliers to snap off the supports. They should break away cleanly. If any small stubs remain, trim them with flush cutters.

---

## Step 2: Removing bottom support material

Flip the housing over. Remove the support material from the four feet locations on the bottom, as shown below.

Bottom support locations

These supports are small and should be easy to remove using a flat tool or your fingernail.

---

**Congratulations!** You have completed the housing preparation. Before continuing to the next chapter, take a moment to verify the following:

- [x] All top support material has been removed from the inside of the housing
- [x] All bottom support material has been removed from the four feet locations
- [x] No leftover stubs are sticking out that could interfere with component placement

!!! note "Check your work"
    Run your fingers along the inside of the housing to make sure no leftover support material is sticking out. Any remaining stubs can interfere with component placement later on.

Removed support material

---

[:octicons-arrow-right-24: Chapter 3: Housing assembly](chapter-3-housing-assembly.md){ .md-button .md-button--primary }

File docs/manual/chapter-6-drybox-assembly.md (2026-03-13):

---
comments: true
---
[:octicons-arrow-left-24: Chapter 5: DryBase assembly](chapter-5-drybase-assembly.md){ .md-button }

# Chapter 6: Drybox assembly

In this chapter you will modify the cereal container to work with your DryBase. This chapter takes roughly 15-30 minutes to complete. By the end of this chapter, your DryBase will be ready for use, including printing directly from the container while drying.

!!! note "Compatible containers"
    The DryBase has been tested and verified with two cereal containers: the **[Wildone](https://www.amazon.nl/dp/B07NP98YKY){:target="_blank"}** (recognizable by its three smaller grooves, left image) and the **[GoMaihe](https://www.amazon.nl/dp/B08JTH2NZJ){:target="_blank"}** (recognizable by its wider narrow section, right image). Both can be found on Amazon. All performance specifications for the DryBase, including maximum temperature and drying times, are based on testing with these two containers.

    Other containers may also be compatible, provided they meet the following requirements:

    - The container has a capacity of ~4 litres
    - The container opening (lid) is exactly 6cm in diameter
    - The small lid cap can be fully removed, so the container can sit flat on the DryBase

    Note that we **cannot** guarantee that untested containers will reach the same temperatures or drying performance as verified with the two containers above.

Compatible containers

!!! warning "Printing while drying"
    If you plan to use your DryBase while actively 3D-printing with the spool inside the container, we recommend using the **Wildone** container only. The GoMaihe's narrower section may not provide enough clearance for a spool during printing. **Always** verify this yourself before use.

Chapter 6 result

## Step 1: Preparing the drybox

The image below is divided into two sections. The **blue box** shows what you need to provide yourself. The **green box** shows the parts included in your DryBase kit.

**You will need to provide yourself** *(blue box):*

- 1x 4L cereal container
- 1x M10 wrench
- 1x 4mm drill bit *(to drill through soft plastic)*
- 1x 9mm drill bit *(to drill through soft plastic)*
- 1x drilling machine
- Cloth

**What's included in your kit** *(green box):*

- Drybox parts *(from the Drybox parts bag)*

Step 1 parts

**a.** Open the Drybox parts bag and locate the 3D-printed spool holder and the small parts bag, as shown in the image below.

Spool holder and small parts

**b.** Take the shafts and bearings from the small parts bag and insert them into the dedicated sockets on the spool holder as shown in the image below. Press down in the direction indicated by the red arrow until you hear and feel a click. This confirms the shaft is fully seated in the socket.

Shaft insert

After installing both shafts, the result should match the image below.

Shafts installed

**c.** Take the cereal container and remove the lid. Then remove the small circular cap from the centre of the lid by sliding it outward in the direction indicated by the arrow in the image below. The cap should come off without much effort.

!!! warning "Do not use a sharp tool to remove the cap"
    Apply pressure with your fingers only to avoid damaging the lid.

Remove cap

**d.** Insert the spool holder with shafts into the opening of the cereal container lid, as shown in the image below. Set this assembly aside for now.

Spool holder in lid

**e.** Drill a 4mm pilot hole at each of your chosen locations on the side of the container, as shown in the images below. These holes will serve as the filament exit ports.

!!! note "Hole placement"
    Position the hole tangent to the side of the spool to minimise pulling friction on the filament during printing. The six recommended locations are indicated in the image below with red arrows. Note that the kit includes enough parts for a **maximum of 2 holes**.

Hole locations

Drilling

**f.** Switch to the 9mm drill bit and widen all 4mm pilot holes, as shown in the image below.

Widen hole

**g.** Remove any remaining burrs or plastic debris from the holes using a craft knife or your fingernail. The result should match the image below.

Clean hole

**h.** Take the 2x PC4-M10 pneumatic fittings and 2x rubber grommets from the small parts bag and assemble them as shown in the images below.

Fitting assembly

**i.** Insert the assembled pneumatic fittings into the drilled holes from the outside of the container. Using your M10 wrench, tighten them until secure.

!!! warning "Do not overtighten"
    The container is made of soft plastic and can crack under excessive force. Tighten until the fitting sits firmly in place and stop.

Fitting install

**j.** From inside the container, thread the 3D-printed closing fasteners onto the M10 threads of the pneumatic fittings and tighten by hand until snug.

!!! warning "Do not overtighten"
    Tighten until the fastener sits firmly against the inside wall of the container and stop.

Fastener parts

Fastener install

After tightening both fasteners, the result should match the image below.

Fasteners result

**k.** Bend the rubber grommet over the pneumatic fitting to close it off, as shown in the images below. This keeps the container sealed when the filament is not in use.

Grommet close

!!! note "Did you know?"
    You can insert the end of your filament into the rubber grommet to keep it easily accessible for your next print. When you open the grommet, the filament comes with it, so there's no need to open the entire container. See the images below.

Filament tip

**l.** Place your filament spool into the container and place the drybox onto the DryBase. Make sure the 6cm opening of the drybox aligns with the container adapter on top of the DryBase, as shown in the images below.

Place drybox

---

**Congratulations!** You have fully assembled both the DryBase and the drybox.

Your setup is now complete and ready for use. To print while drying, use the included PTFE tube to connect the drybox to your 3D printer. When storing the drybox, make sure to close both grommets and reinstall the round cap on the container lid to keep the container sealed. Take a moment to verify the following:

- [x] Both shafts are seated in the spool holder with an audible click
- [x] The spool holder is inserted into the lid opening
- [x] The pneumatic fittings are secured with the wrench and closing fasteners
- [x] The grommets are closed when not in use
- [x] The drybox sits flat on the DryBase with the opening aligned

!!! note "Need help?"
    If you run into any issues, reach out at [support@filametric.com](mailto:support@filametric.com). We're happy to help.

DryBase and drybox complete

---

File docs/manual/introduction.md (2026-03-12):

# Introduction

The Filametric DryBase

The DryBase was designed for one purpose: to dry filament properly. Not just warm it up, but actually remove moisture, at temperatures high enough to make a real difference for engineering-grade materials. At the same time, we wanted it to stay compact and compatible with the well-known affordable cereal containers the community already loves. The result is DryBase.

These instructions will guide you through the full assembly process, step by step. Each chapter covers a distinct part of the build, and every step includes reference images so you always know what a correct result looks like.

## What's ahead

The assembly is split into six chapters. You'll start by checking your kit contents, then work your way through preparing, building, and finally putting everything together.

| | Chapter | What you'll do |
|---|---|---|
| 1 | [Unboxing & checking components](chapter-1-unboxing.md) | Verify your kit contents and gather the required tools |
| 2 | [Preparing the DryBase housing](chapter-2-preparing-housing.md) | Remove all support material from the 3D-printed housing |
| 3 | [Housing assembly](chapter-3-housing-assembly.md) | Install the PSU, exhaust fan, circuit boards and display into the housing |
| 4 | [Heating unit assembly](chapter-4-heating-unit-assembly.md) | Assemble the heating element enclosure, blower fan, container adapter and exhaust port onto the baseplate |
| 5 | [DryBase assembly](chapter-5-drybase-assembly.md) | Connect all cables, install the heating unit into the housing and power on |
| 6 | [Drybox assembly](chapter-6-drybox-assembly.md) | Modify the cereal container and install the spool holder, filament exit ports and pneumatic fittings |

## Before you begin

You will need a clean, flat surface and about **3 hours** to complete all chapters. The kit includes most of what you need. A small number of items are not included and are listed in [Chapter 1](chapter-1-unboxing.md) for the DryBase and [Chapter 6](chapter-6-drybox-assembly.md) for the drybox.

!!! warning "Take your time"
    If something doesn't fit or look right, stop and check before continuing. A little patience here saves a lot of trouble later.

!!! note "Need help?"
    If you run into any issues, reach out at [support@filametric.com](mailto:support@filametric.com). We're happy to help.

---

[:octicons-arrow-right-24: Chapter 1: Unboxing & checking components](chapter-1-unboxing.md){ .md-button .md-button--primary }

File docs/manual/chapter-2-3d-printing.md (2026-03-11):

# Chapter 2 — 3D Printing

<!-- TODO: Add content -->

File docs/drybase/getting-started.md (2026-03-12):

# Getting Started

This page is coming soon.

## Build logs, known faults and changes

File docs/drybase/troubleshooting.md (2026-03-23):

# Troubleshooting

This page is coming soon.

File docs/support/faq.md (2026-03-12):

# Frequently Asked Questions

This page is coming soon.

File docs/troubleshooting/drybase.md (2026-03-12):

# DryBase Troubleshooting

This page is coming soon.

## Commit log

2026-03-11 Fix navbar: restore full names and force all tabs visible
    - Revert tab labels to full names (Assembly Manual, DryBase Firmware, etc.)
    - Override MkDocs Material tab hiding with CSS !important rules
    - Force all tab items to always be visible regardless of active page
2026-03-11 Revert to native MkDocs Material navigation.tabs
    - Remove custom template override (was breaking sidebar)
    - Use native navigation.tabs + navigation.tabs.sticky
    - Let MkDocs Material handle both tabs and sidebar natively
2026-03-11 Add homepage grid cards and separate 3D Printing section
    - Homepage with 6 card widgets linking to each section
    - Move 3D Printing out of Assembly Manual into own nav tab
    - Renumber assembly chapters (2-5 without 3D printing)
    - Add Print Files page under 3D Printing
2026-03-11 Restructure assembly manual chapters
    - Rename and renumber chapters to match new structure
    - Add Chapter 2 (Preparing housing) and Chapter 6 (Drybox)
    - Use consistent "Chapter N: Title" format
2026-03-11 Add assembly manual introduction content
2026-03-11 Improve introduction: add chapter descriptions and continue button
2026-03-11 Add chapter 2 content: preparing the DryBase housing
2026-03-11 Add back buttons to chapters, remove redundant text in ch2
2026-03-11 Move back button to top of chapters
2026-03-11 Rename introduction heading from Assembly Manual to Introduction
2026-03-11 Add Chapter 3 Step 2: Installing the exhaust fan
2026-03-11 Add Chapter 3 Step 3: Connecting power cables to the PSU
2026-03-11 Update Step 3 images: combine parts/cables, replace screw photos
2026-03-11 Combine orientation and cable images into single photos
2026-03-11 Add Chapter 3 Step 4: Connecting PSU to the power board
2026-03-11 Add Chapter 3 Steps 5-7: PSU installation, wiring, rubber feet
2026-03-11 Move power board note before rubber feet image
2026-03-11 Add Chapter 3 Step 8: Connecting display and cables to Main & Sensor board
2026-03-11 Add Chapter 4 intro and Step 1: Preparing the heating element enclosure
2026-03-11 Add Chapter 4 Step 2: Installing heating element assembly onto baseplate
2026-03-11 Add Chapter 4 Step 3: Installing blower fan, container adapter and exhaust port
2026-03-11 Add Chapter 5: DryBase Assembly - installing heating unit into housing
2026-03-11 Replace ch5 result, parts and heater-cable images
2026-03-12 Improve FPC cable warning and move before image in ch3 step 9b
2026-03-12 Fix chapter navigation buttons visibility in dark mode
2026-03-12 Add hover states for navigation buttons in dark mode
2026-03-12 Adjust forward button hover to lighter orange in dark mode
2026-03-12 Use darker orange for forward button hover in dark mode
2026-03-12 Add Chapter 6: Drybox assembly - modifying cereal container for DryBase
2026-03-12 Fix 3D Printing guide link in ch1
2026-03-12 Add 3D Printing section with housing guide, downloads and card grid
    [DryBase_Housing_3MF_File.3mf, DryBase_Housing_STEP_File.STEP]
2026-03-12 Fix image path and link in 3D printing card grid
2026-03-12 Fix housing card link path
2026-03-12 Restructure housing guide: add image, print time, reorder sections
2026-03-12 Add layer height and build plate to workspace settings
2026-03-13 Add Giscus comments to manual chapters and housing guide
2026-03-13 Add warning about untested materials in housing guide
2026-03-13 Specify Bambu Lab PLA Basic as tested filament for housing
2026-03-13 Clarify PLA recommendation in housing guide
2026-03-20 Rename flat-headed screws to round-headed screws
2026-03-22 Add DryBase and Drybox categories to 3D printing section
2026-03-22 Add complete 3D printing section with all component guides
2026-03-23 Add STEP downloads, rename files with Filametric prefix, update license text
    [Filametric_Closing_Fastener_STEP.step, Filametric_Container_Adapter_STEP.step, Filametric_Grommet_STEP.step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]
2026-03-23 Add disclaimer to license section on all 3D printing pages
2026-03-23 Add disclaimer with terms of use link to 3D printing pages
2026-03-23 Clarify bed temperature settings are specific to Fiberon PA6-GF20
2026-03-23 Standardize drying warning title, add printer-specific settings note for PA6-GF
2026-03-23 Fix UTF-8 encoding, update material warnings for ABS and PA6-GF parts
2026-03-23 Update housing print time to 6h 8m
2026-03-23 Add 0.4mm nozzle to all parts, add wipe while retraction to PA6-GF parts
2026-03-23 Add chamber temperature setting to PA6-GF filament profiles
2026-03-23 Update moist air exhaust port print time to 7m
2026-03-23 Update baseplate print time to 1h 41m
2026-03-23 Update container adapter print time to 33m
2026-03-23 Add 3MF and STEP downloads for all components
    [Filametric_Closing_Fastener_3MF.3mf, Filametric_Container_Adapter_3MF.3mf, Filametric_Grommet_3MF.3mf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]
2026-03-24 Clarify license: selling printed parts is also not permitted
2026-03-24 Remove part cooling fan from PA6-GF filament settings (is default)
2026-03-24 Update PA6-GF 3MF files with corrected cooling settings
    [Filametric_Closing_Fastener_3MF.3mf, Filametric_Heating_Element_Bottom_Cover_3MF.3mf, Filametric_Heating_Element_Top_Cover_3MF.3mf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]
2026-03-24 Add sliced result images to housing and container adapter, fix housing subsections
